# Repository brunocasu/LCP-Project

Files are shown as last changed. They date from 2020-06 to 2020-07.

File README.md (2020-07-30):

# Low-Cost Cubesat Prototype (LCP)
(EN) This repository contains the Hardware and Software Projects to construct and operate a low cost nanosatelite prototype (LCP) developed by the electrical engineering students at the Centro Universitário FEI (Brazil), as part of the Electrical Engineering Bachelor's Thesis Project.

(PT) Este repositório comporta os Projetos de Hardware e Software para construção e operação de um protótipo de baixo custo de nanosatélite (LCP) desenvolvido pelos alunos de engenharia elétrica do Centro Universitério da FEI, como parte do projeto de conclusão de curso de Bacharel em Engenharia Elétrica.

## Hardware Project for the LCP platform
(EN) The hardware project comprehends electrical schematics, PCB designs as well as the BOM (Bill of Materials) intended for its construction.

(PT) O projeto de hardware compreende os esquemas elétricos, design das PCBs e também seu BOM (Lista de Materiais) destinados para sua construção.

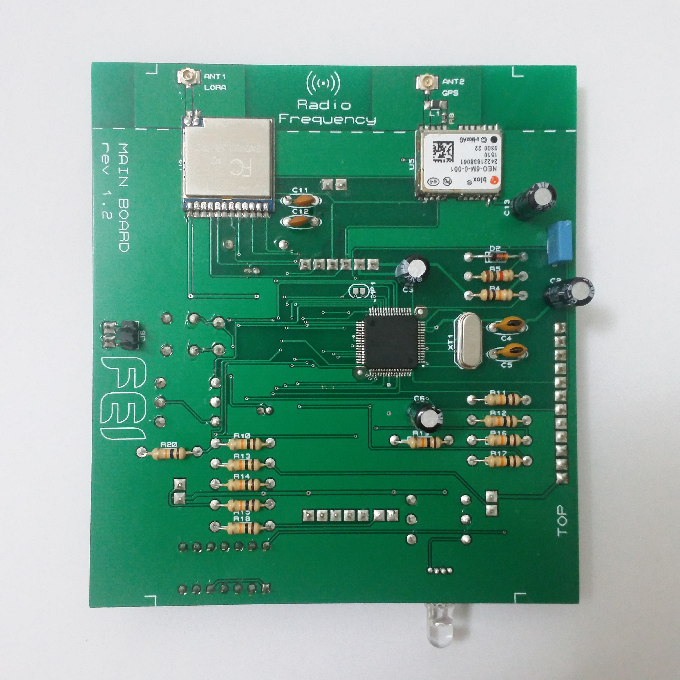
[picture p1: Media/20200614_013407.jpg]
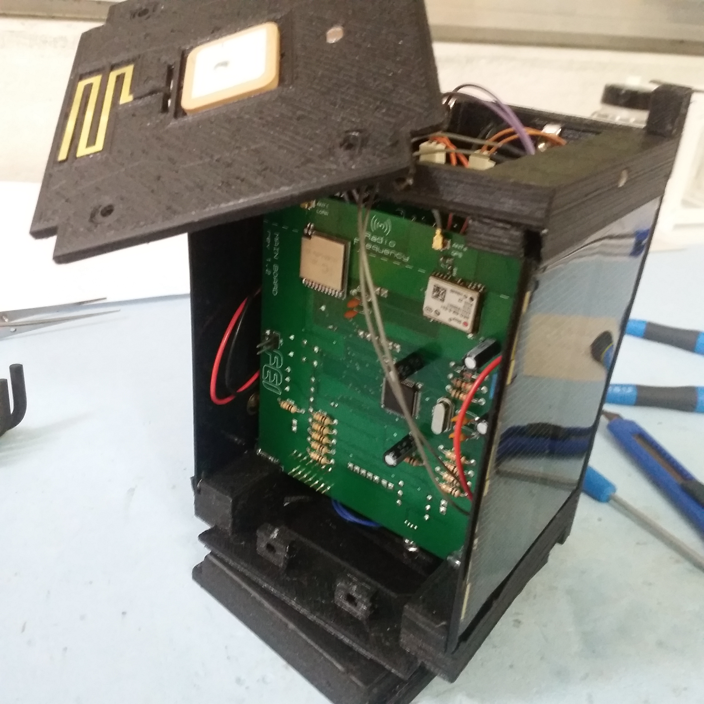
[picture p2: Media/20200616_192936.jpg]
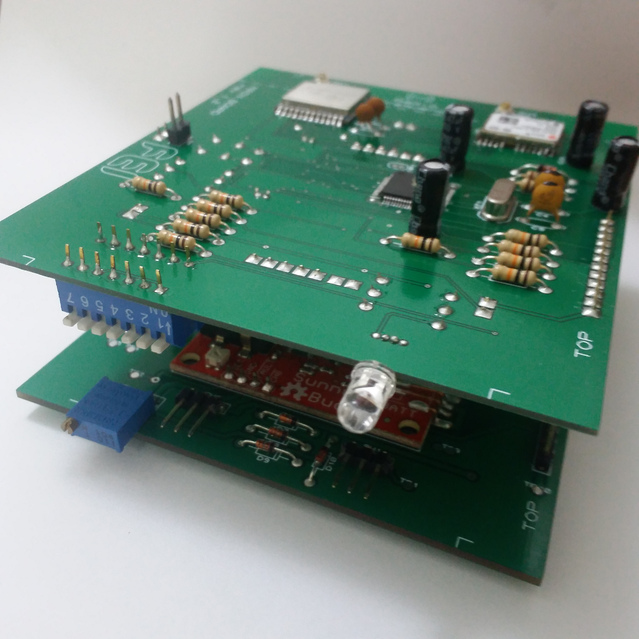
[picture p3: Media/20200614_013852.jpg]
  

## Flight Software for the LCP platform
(EN) The target MCU is the Renesas RL78 - R5F100LE, using the RL78 IAR programming and development tool (IAR IDE for the RL78).
In addition the ground station software is available to RaspberryPi and OrangePi platforms (tests were performed using a Pi Zero W and OrangePi One models).

(PT) O MCU objetivo de utilização foi o Renesas RL78 - R5F100LE, havendo sido utilizado o RL78 IAR para fins de programação e desenvolvimento (IAR IDE for the RL78).
Ainda, o software da estação terrena encontra-se disponível para as plataformas RaspberryPi e OrangePi (testes realizados utilizando os modelos Pi Zero W e OrangePi One).

Execution Example:
```
>>> import lcp

LCP script has started.
Type in:
lcp.diconnect() to disconnect
or CTRL+C to exit.

SX1276 Configuration OK
FLOOR RSSI: - 44.0 dBm

>>> lcp.send_sensor_read ()

INFORMATION FRAME SENT: REQUEST SENSOR READINGS
SEQUENCE NUMBER N(R): 0x1
WAITING FOR REPLY...

MESSAGE RECEIVED (RESPONSE)
REPLY OF INFORMATION FRAME FROM: FEILCP | SEQUENCE N(S): 0x1 | PAYLOAD CODE: 0xa1
SENSORS READING REPLY:
NTC0:             21.81      C
NTC1:             23.30      C
LDR0:             3.13       lux
LDR1:             6.18       lux
LDR2:             2.20       lux
LDR3:             0.09       lux
LDR4:             1.30       lux
LDR5:             4.13       lux
VOLTAGE:          3.28       V
CURRENT:          2.10       mA
BMP280 Temp:     32.04      C
BMP280 Pres:     175.11     kPa
BMP280 Pres:     1.31       mmHg
TIME TO RESPOND: 46.9 ms
RECEIVED SIGNAL STRENGTH INDICATION: - 55.5 dBm
******************************************************************
```

Demonstration: (Watch on YouTube)
Low-Cost Cubesat (https://youtu.be/lgCKG8bld8Y "Low-Cost Cubesat Prototype - Click to Watch!")

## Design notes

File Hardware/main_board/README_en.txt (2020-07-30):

---------------------------------------README----------------------------------------
This schematic is part of the LCP project

---------------------------------------AUTHOR----------------------------------------
@Author		Bruno Duarte

---------------------------------------VERSION---------------------------------------
@version	main_board_v1.x
@brief		main board hardware project

v1.0	Original project for professional manufacturing
v1.1	Simplified project for home made production
v1.2	Dimensional changes to adequate for the available production method

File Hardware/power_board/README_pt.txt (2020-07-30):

---------------------------------------README----------------------------------------
Este esquemático é parte do projeto LCP

---------------------------------------AUTHOR----------------------------------------
@Autor		Bruno Duarte

---------------------------------------VERSION---------------------------------------
@versão		power_board_v1.x
@descrição	projeto PCB da placa de potência

v1.0	Projeto original para produção profissional
v1.1	Projeto simplificado para produção artesanal
v1.2	Alteração de dimensões para adequação ao processo de fabricação disponível

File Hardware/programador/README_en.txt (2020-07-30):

---------------------------------------README----------------------------------------
This schematic is part of the LCP project

---------------------------------------AUTHOR----------------------------------------
@Author		Bruno Duarte

---------------------------------------VERSION---------------------------------------
@version	programador_v1.2
@brief		programmer board hardware project

----------------------------------------NOTES----------------------------------------
#1 Revised project for professional manufacturing

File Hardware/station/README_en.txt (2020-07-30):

---------------------------------------README----------------------------------------
This schematic is part of the LCP project

---------------------------------------AUTHOR----------------------------------------
@Author		Bruno Duarte

---------------------------------------VERSION---------------------------------------
@version	station_v1.2
@brief		shield project for incorporate LoRa on RaspberryPi/OrangePi

----------------------------------------NOTES----------------------------------------
#1 Revised project for professional manufacturing

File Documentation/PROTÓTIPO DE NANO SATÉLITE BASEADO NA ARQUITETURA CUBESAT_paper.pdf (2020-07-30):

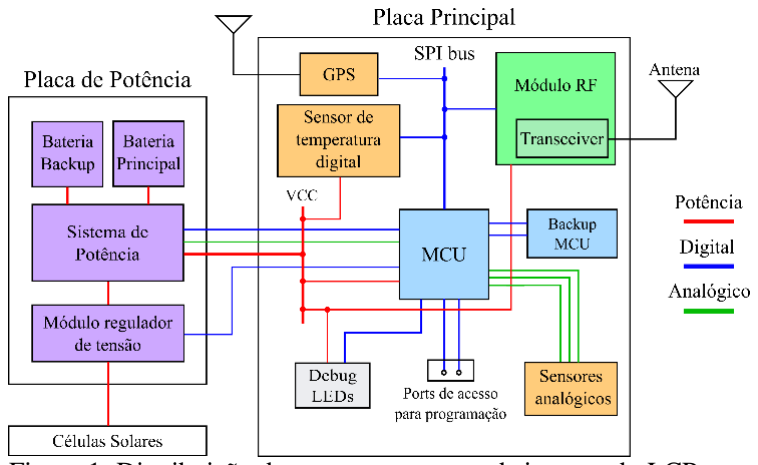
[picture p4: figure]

São Bernardo do Campo – 2020

## PROTÓTIPO DE NANO SATÉLITE BASEADO NA ARQUITETURA CUBESAT PARA RADIOCOMUNICAÇÃO

Bruno Augusto Casu Pereira de Sousa, Bruno Duarte dos Santos, Rodrigo Yudji Katagiri de Oliveira, Victor Garcia Palacios Centro Universitário FEI

Resumo: O avanço das novas tecnologias do ramo aeroespacial foi impulsionado de forma significativa pela evolução dos sistemas de telecomunicação, garantindo aos satélites modernos grande capacidade computacional, mas com a vantagem de miniaturizar os dispositivos, reduzindo os custos das missões. Nesse contexto, o desenvolvimento do padrão CubeSat pela NASA permitiu a expansão de novos estudos e inovações na área, principalmente para as instituições acadêmicas e de pesquisa, ao passo que o modelo permite implementações de baixo custo e
arquiteturas | simplificadas. | O | objetivo | do | projeto
apresentado é estudar e implementar a arquitetura CubeSat no desenvolvimento de um protótipo de nano satélite, designado como Low Cost CubeSat Prototype (LCP). Como resultado, será apresentado um sistema independente com um módulo de comunicação em radiofrequência, permitindo o controle do protótipo e monitoramento dos dispositivos de telemetria por um conjunto de computadores remotos.

### 1. Introdução

Com o aumento da relevância de novos projetos de CubeSats por universidades, e a acessibilidade em relação aos custos de produção e lançamento, comparado a satélites convencionais, se vê um aumento no interesse do lançamento deste formato de satélite. Com isso, a necessidade de uma prova de conceito em relação ao desenvolvimento e produção dos satélites de classe pequena (nano satélites e micro satélites) utilizando tecnologias comerciais comuns se tornou uma necessidade, além de proporcionar diversas inovações na área.
Levando em consideração que um projeto de Cubesat normalmente possui uma duração de 18 a 24 meses para ser desenvolvido, montado, testado e entregue para lançamento [1]; e envolve investimentos elevados, atingindo até 250 mil reais, uma abordagem diferente foi usada na concepção do projeto, visando a produção de uma plataforma de desenvolvimento, que pudesse ser expandida.
O protótipo concebido no projeto então foi designado como Low Cost CubeSat Prototype (LCP), e envolveu um tempo de produção relativamente menor, em torno de 12 meses, além do custo ser reduzido para 3 mil reais, algo mais acessível para instituições de ensino no Brasil. Devido ao tempo e o custo serem menores em comparação ao comum, foi necessário realizar certas abordagens não-convencionais, como o uso de componentes COTS além de métodos para prototipagem simplificados. Portanto, para a composição do LCP foram incorporados módulos de desenvolvimento do segmento de IoT (rádios e sensores), assim como placas de circuito impressas que possam ser fabricadas em fresas de gravação.
Mesmo com certas limitações, ainda se teve um cuidado de seguir parâmetros da NASA para o desenvolvimento do
LCP, | assim | extraindo | de | componentes | eletrônicos
convencionais o máximo possível para se obter uma plataforma com comunicação em Radiofrequência (RF) e com suficiente autonomia. Ainda foram implementados sistemas de redundância no computador de bordo, com backup de CPU, e no sistema de alimentação, utilizando duas baterias. Para uma rápida prototipagem e uma modularidade do sistema, sua parte mecânica foi produzida por impressoras 3D, ainda seguindo os guias de design padrão, mas com certas adaptações e optimizações para os componentes, assim como um nível de flexibilidade para futuras modificações.
Para garantir o funcionamento do sistema geral do LCP e demonstrar sua eficiência, ainda foram realizados certos testes de bancada, focando principalmente na operação do software de voo e comunicação com a estação terrena, demonstração da potência efetiva das células solares e da autonomia das baterias, assim como as funcionalidades dos sistemas de redundância. Nos itens abordados neste texto,
serão | descritos | o | desenvolvimento | e | as | soluções
apresentadas para a plataforma desenvolvida, assim como os testes providenciados.

### 2. Estrutura geral e hardware mecânico

A composição e distribuição dos subsistemas do protótipo foram baseadas em estruturas previamente definidas nas especificações e outros projetos de CubeSat que foram desenvolvidos e testados [2][3]. Essencialmente o sistema de um nano satélite deve conter cinco funções, em adição à estrutura mecânica, que então definem a plataforma: Subsistema de alimentação, Dispositivos de telemetria, Subsistema de comunicação, CPU e Controle de temperatura. No caso específico do LCP, o controle de temperatura das baterias foi repassado para o computador central, de forma a simplificar o sistema de controle exigido.

Figura 1: Distribuição dos componentes e subsistemas do LCP.

Na Figura 1 é possível notar a distribuição dos componentes na arquitetura do LCP, compondo os subsistemas básicos da plataforma. A integração dos componentes foi complementada com o desenvolvimento de um frame customizado para o projeto.

A estrutura mecânica foi baseada nos aspectos e definições da NASA em relação ao formato e composição do frame para o CubeSat [4]. O padrão então denomina o tamanho de um único cubo a unidade U, onde um CubeSat 1U, ou 1 cubo, possui 100 milímetros por 100 mm por 100 mm. As demais denominações (2U, 3U) possuem um incremento de 100 mm na altura (eixo z) para cada adição de uma unidade. Estas derivadas do tamanho U, no entanto, requerem invariavelmente que uma de suas faces possua 100 x 100 milímetros, devido ao modo da construção do instrumento de lançamento dos satélites, este denominado Poly-Pico Orbital Deployer ou P-POD, que possui um espaço interno de 100x100x300 milímetros.
Considerando | que | o | frame | do | protótipo | foi
desenvolvido com certas adaptações, o design final da estrutura mecânica do LCP acabou por não atender rigorosamente os padrões de altura, denominados pela unidade U. Isso ocorreu por conta das placas solares adquiridas, além da necessidade de utilizar placas PCB maiores para comportar os módulos usados. Em todo caso, as medidas de larguras, sendo as dimensões críticas, mantiveram o padrão de 100 mm de lado, ainda definindo o protótipo na classe de nano satélites. Eventualmente um aumento na classe do protótipo para 2U pode ser considerado para futuras expansões, de forma a manter o protótipo nos padrões requeridos.

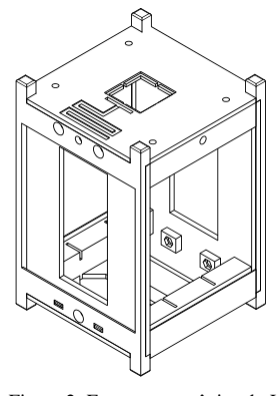
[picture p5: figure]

Figura 2: Estrutura mecânica do LCP.

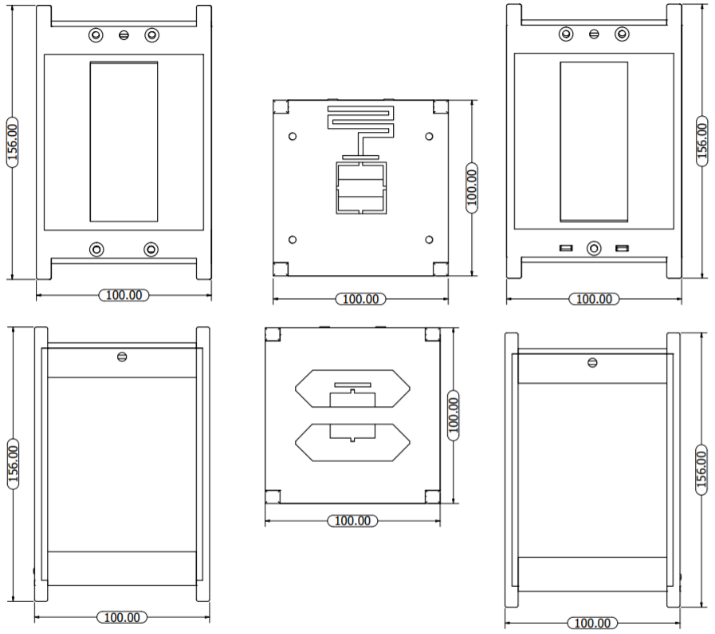
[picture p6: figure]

Figura 3: Vista das peças do frame customizado do LCP.

Os suportes das partes eletrônicas nesse design foram feitos de modo em que a montagem fique unificada, além de otimizar o centro de massa do dispositivo e seu espaço interno. Componentes de RF que necessitam ficar na superfície externa do cubo, como as antenas, se encontram em recessos no topo, sendo mantidos presos pelo próprio material. Essa estratégia também foi usada para posicionar as placas solares, que ficam ao centro das áreas laterais, e as placas principais com seus standoffs embutidos, ajudando também na rigidez mecânica do projeto.
O design mecânico em sua totalidade foi confeccionado em impressoras 3D, por sua velocidade de prototipagem combinadas a sua alta precisão, habilitando assim mudanças frequentes de medidas e designs. O material usado para sua composição foi o Tritan HT, um copoliester 3d fila, possuindo uma alta dureza e resistências a temperaturas, este sendo um outro desvio as recomendações da NASA que indica a construção de sua estrutura por alumínio 7075, 6061, 5005 ou 5052.

### 3. Subsistema de potência

O sistema de potência do LCP consiste em uma junção de quatro placas solares ligadas em paralelo e duas baterias de polímero de lítio, também denominadas Lipo. As partes então foram associadas ao módulo regulador de tensão SunnyBuddy da SparkFun [5], que implementa tecnologia de Maximun Power Point Tracking (MPPT) para maximizar a eficiência das células solares em conjunto com o sistema de baterias.
O módulo então provê as funcionalidades necessárias para o gerenciamento do fornecimento de energia ao sistema principal, de forma a garantir o funcionamento da plataforma. A placa SunnyBuddy também possui circuito de proteção para as baterias inseridas no sistema de potência, sendo de grande importância para a utilização de baterias com lítio em sua composição, visto que uma falha poderia causar sobrecargas, danificando o hardware.

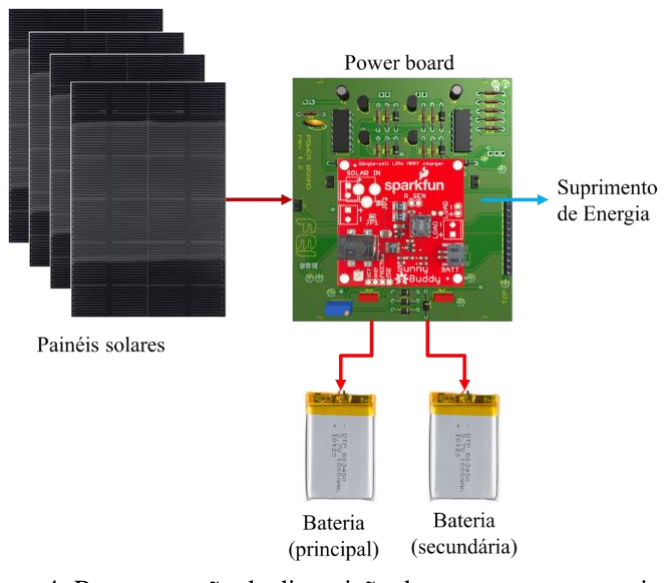
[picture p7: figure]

Figura 4: Representação da disposição dos componentes no sistema de potência.

As baterias escolhidas têm carga de 2600mAh, e foram incorporadas na placa de potência por um circuito de troca dedicado, desenvolvido especificamente para a aplicação no LCP. Essa implementação garante o funcionamento em redundância, onde a bateria secundaria se encontra em cold standby, e, caso ocorra uma eventual falha que danifique a bateria principal ou se sua eficiência caia drasticamente se tem a troca para a bateria secundaria, assim estendendo a longevidade da bateria assim como a sua resistência a falhas. O circuito ainda disponibiliza ao controlador da estação a possibilidade de atuar remotamente na supervisão e troca das baterias do sistema de potência, elevando a disponibilidade da plataforma.

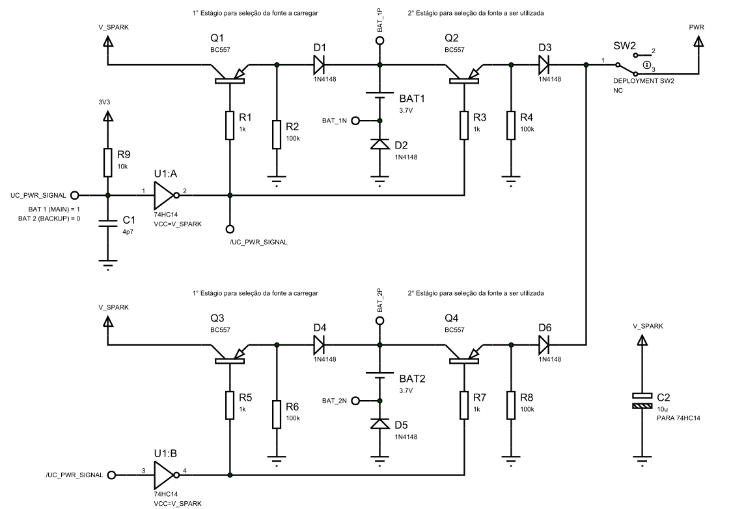
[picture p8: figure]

Figura 5: Circuito de troca de baterias.

Dadas as considerações da implementação do sistema de alimentação, a placa PCB foi confeccionada para atender os requisitos de corrente necessário e comportar os módulos usados no sistema com as células solares e as baterias. A Figura 6 ilustra a placa desenvolvida para o LCP com os componentes inseridos. Nota-se ainda que foi utilizado um barramento de pinos para garantir a conexão dos pinos de potência com a placa principal, onde os outros subsistemas e dispositivos se encontram.

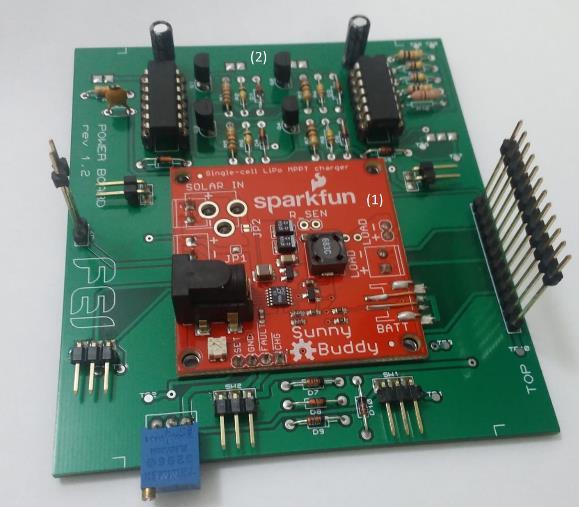
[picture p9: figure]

Figura 6: Placa de potência do LCP.

### 4. Dispositivos de telemetria

Como forma de demonstrar a manutenção e supervisão dos subsistemas agregados no LCP, cinco tipos de sensores foram dispostos: temperatura, pressão, luminosidade, tensão e corrente. O principal componente de telemetria do protótipo é o sensor digital de temperatura BMP280 da Bosch [6], que foi implementado para prover leituras, com precisão de 0,01 °C, da temperatura do ambiente. As leituras e a programação desse dispositivo são realizadas pela interface serial do sensor, através de um barramento SPI (em concordância com a arquitetura computacional do LCP). O

BMP280 ainda prove leitura de pressão do ambiente, sendo um complemento interessante para a avaliação das condições de operação do protótipo nos testes.
Além do sensor digital, um sensor de corrente e outro de tensão foram usados para monitorar o comportamento do sistema, em específico das condições da placa de potência. Esses sensores providenciam leituras analógicas ao computador central do nível de tensão fornecido à placa principal e a corrente de operação, e tem relevância na garantia da integridade dos componentes usados na alimentação. Além disso, as baterias da placa de potência são monitoradas com sensores analógicos de temperatura (NTC), de forma a os controladores da estação no solo as condições de operação.
O subsistema de telemetria ainda foi complementado com a inserção de sensores e luminosidade (LDR) nas laterais do cubo, de forma a identificar as regiões com maior intensidade luminosa. Esses sensores têm relevância pois disponibilizam dados de luminosidade que podem ser computados para uma análise estatística do comportamento de carga das baterias. Os dados de luminosidade então fazem parte do Payload do LCP.
Finalmente ainda foi avaliado o uso de um sistema de GPS em conjunto com o módulo de comunicação, adicionado mais informações relevantes no link com as estações. O GPS então foi adicionado à plataforma como complemento do Payload disponibilizado.

### 5. Subsistema de comunicação

O módulo de comunicação do CubeSat compõe o subsistema mais crítico do projeto, considerando que seu funcionamento deve prover uma comunicação estável e robusta com as estações, além de permitir o envio de uma taxa considerável de dados de forma a atender a composição do payload da plataforma [7]. Para o sistema de comunicação do LCP, sua composição foi modelada para o uso de um transceiver LoRa de baixo consumo SX1276, da Semtech [8][9]. O rádio está presente em um módulo wireless da NiceRF, otimizado para operação em 915 MHz [10]. Além da estrutura de RF, o módulo usado facilita a integração desse subsistema com o computador central do LCP, visto que o componente disponibiliza uma interface de acesso serial aos registradores do SX1276, através de um barramento SPI, assim como o sensor digital do subsistema de telemetria.
Com isso, os parâmetros do rádio são definidos com a escrita nos registradores do SX1276, através desse barramento serial; em adição, os dados da comunicação também são transmitidos pelo SPI, usando uma fila FIFO no DFE do rádio para garantir a eficiência do transceiver na composição e envio dos pacotes, assim como no recebimento e informe da chegada de mensagens.
Para a comunicação do LCP , o rádio foi configurado com a maior potência de transmissão, em 20 dBm, além do uso do modem FSK do transceiver. A taxa padrão de transmissão foi estabelecida para 4,8 kbps, com separação de portadoras em 5 kHz. Nessa configuração, portanto, a sensibilidade esperada então se mantém em torno de -110 dBm, permitindo um alcance considerável para a comunicação do protótipo.

Além dos parâmetros de transmissão do rádio, o SX1276 permite o envio das informações em diferentes formatos. O link com as estações remotas foi implementado usando um protocolo com pacotes de tamanho fixo em 64 bytes. Nesse pacote ainda foi habilitado a implementação de um código de correção de erros CRC pelo transceiver, além da utilização de uma palavra de sincronização e redundância 4/5. Com isso a comunicação entre os rádios foi mantida com considerável robustez e taxa de transmissão de dados. Em complemento com o pacote do SX1276 o LCP ainda usa um protocolo de acesso de link. Devido ao tempo disponível para desenvolvimento do software, foi decido utilizar uma implementação própria do protocolo de link de acesso AX.25 [11], extraindo as características principais de sua estrutura, e adaptando certos aspectos para o subsistema de comunicação do LCP. Dessa forma, a camada de acesso permite o envio de endereços, bytes de controle e supervisão, além de números sequenciais nas mensagens, atribuindo boa confiabilidade ao link do protótipo com as estações remotas. Na figura a seguir está exemplificado uma sequência de mensagens padrão no link, ilustrando a organização das numerações das mensagens a partir do protocolo AX.25 adaptado.

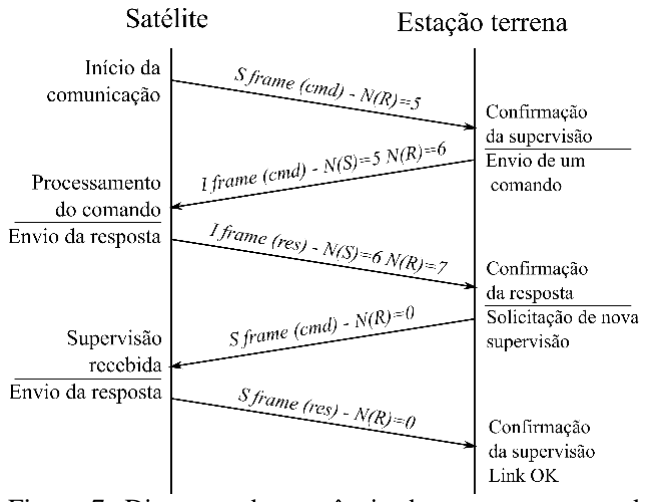
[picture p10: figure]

Figura 7: Diagrama de sequência de mensagens trocadas no link de comunicação entre o LCP e a estação terrena.

No contexto da comunicação do LCP, ainda foi elaborado uma série de funções adicionais, sendo inseridas no espaço de informação disponível no frame do protocolo de acesso. Um segundo protocolo então foi implementado (LCP Application Protocol, LAP), providenciando uma camada de aplicação à plataforma. Essas funções extras permitem a obtenção das informações do satélite, leituras de sensores, monitoramento do sistema de potência, além de uma função de envio de mensagens de texto entre estações remotas.

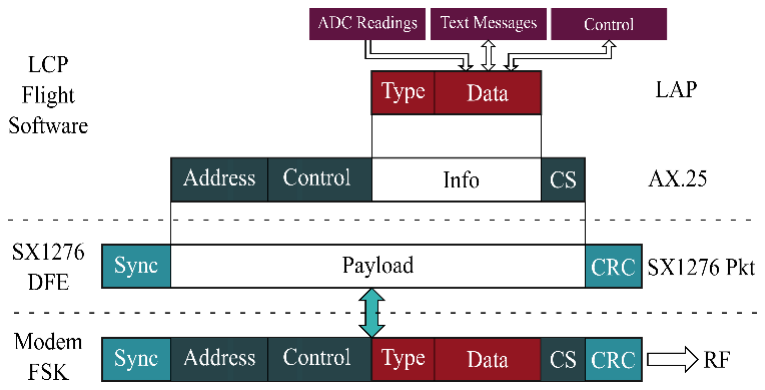
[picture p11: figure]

Figura 8: Divisão das camadas de comunicação o LCP.

Na Figura 8 então é ilustrado o desenvolvimento das camadas de comunicação do protótipo, considerando em última instância a camada física do sinal modulado em FSK e transmitido em RF.
Nota-se ainda na figura que as camadas inferiores são implementadas no hardware do módulo de comunicação usado, ao passo que as camadas superiores da comunicação são resolvidas pelo software de voo do LCP. Com isso a supervisão e comunicação do dispositivo em operação é garantida, considerando que o protótipo envia mensagens regularmente às estações. Da figura ainda é possível notar, ao final do processo, a estrutura final do pacote; que então deve ser modulado em FSK pelo transceiver e enviado às estações.
Como complemento ao hardware do rádio, uma antena monopolo foi adquirida para inserção na face superior externa do cubo, de forma a maximizar o ganho. Essa antena ainda possuiu dimensões reduzidas e montagem de forma plana, facilitando sua inserção no frame do LCP.

### 6. Computador central e software de voo

Como componente central de controle da plataforma, o LCP faz o uso de um microcontrolador, inserido em uma arquitetura de computação em estrela [3], mantendo o Computador de bordo como dispositivo central, ligado aos subsistemas periféricos. O MCU usado no projeto foi escolhido considerando as grandes restrições de consumo de corrente, além da necessidade das interfaces seriais e conversores ADC, de forma a contemplar todas as necessidades da arquitetura estabelecida para o protótipo.
O componente escolhido foi então o modelo RL78 R5F100LG, da fabricante Renesas [12][13]. Esse MCU é da família Ultra Low Power de microcontroladores, e possuiu
características | computacionais | razoáveis | para | o
desenvolvimento e testes da plataforma, como: RAM de 12 kB e memória flash programável de 128 kB, mantendo um consumo de corrente de 4,6 mA na operação normal. Como forma de garantir a confiabilidade do sistema de controle, essa CPU foi instalada com um segundo RL78 em redundância, de forma que caso ocorra uma falha no computador principal, o MCU de backup passa a atuar no controle do sistema.
Da interface do RL78 serão usados ainda um canal serial da Serial Array Unit (SAU) para o SPI da plataforma, e 10 canais ADC para o uso dos sensores analógicos disponíveis.
Considerando | a | disponibilidade | do | sistema | de
computação, o software de voo foi desenvolvido para garantir a manutenção dos dispositivos, o controle dos sistemas e a comunicação do satélite. A linguagem C de programação foi amplamente usada no projeto, em conjunto da plataforma de desenvolvimento IAR IDE [14], específica para os microcontroladores da família RL78.
O software de voo então contempla um driver desenvolvido para configuração e controle do SX1276, um driver para implementação do protocolo de acesso AX.25, um driver para os sensores e dispositivos de telemetria e uma máquina de estados geral (FSM). A FSM implementada então tem o propósito de realizar as chamadas das funções dos drivers realizando as transições dos estados na comunicação (transmitindo ou recebendo) além de manter a supervisão do funcionamento dos sistemas. Os estados definidos na FSM são ilustrados na figura a seguir:

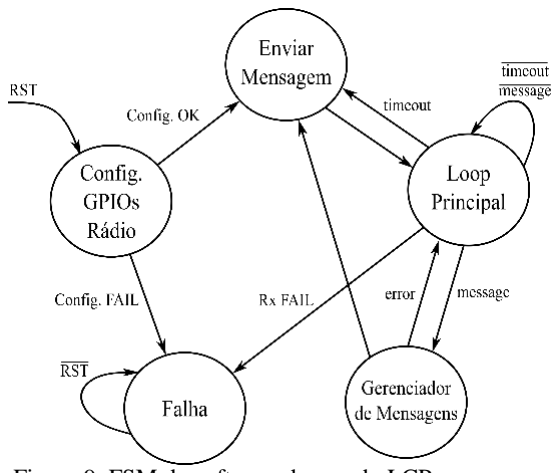
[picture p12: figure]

Figura 9: FSM do software de voo do LCP.
O software, em sua operação normal, inicia o sistema com a configuração dos registradores e periféricos ligados ao computador central (timers, ADCs, canais seriais e interrupções do RL78), além da habilitação dos GPIOs do MCU e a configuração geral dos parâmetros do rádio. Caso essa operação falhe, o sistema é levado a um estado de falha crítica, desabilitando as funções de controle até que um reset externo seja executado. No caso de as configurações serem realizadas com sucesso, o software deve então passar para o estado de envio de mensagens, transmitindo o primeiro comando de supervisão, o que indica as estações que o satélite está pronto para operar. Após o envio dessa primeira mensagem, a máquina de estados passa para o loop principal, onde o rádio é configurado para o modo receptor, aguardando os comandos da estação.
Nesse estado, um contador é ativado, realizando um incremento a cada um segundo, onde, em paralelo, o software verifica a integridade dos sistemas de alimentação. Quando o contador do loop atinge um valor determinado (timeout), uma mensagem de supervisão é automaticamente gerada, identificando que o dispositivo ainda se mantém ativo. Caso ocorra uma falha ou mal funcionamento na alimentação do sistema, a placa da Sparkfun informa o controlador central, que altera o conteúdo das mensagens regulares em sua rotina de supervisão, possibilitando aos controladores que atuem na plataforma com o envio de comandos de controle de hardware.
Em outro caso, onde o sistema ainda está no loop principal, o rádio pode receber uma mensagem proveniente de uma estação. Nessa situação, a máquina de estados é informada através de uma interrupção de hardware (sinal gerado por pinos digitas da interface do SX1276), que identifica o recebimento de um pacote pelo rádio. Assim, o loop é interrompido e a FSM passa para o estado gerenciador de mensagens. Nesse estado, o sistema faz a leitura dos bytes da FIFO do SX1276, recuperando a mensagem recebida e identificando o comando da camada de aplicação. Para tanto, a decomposição das camadas de comunicação competentes ao software é realizada em tempo de operação. Após a identificação, o sistema deve providenciar o conteúdo adequado para a resposta a estação de origem da mensagem. Ao término do processamento do estado gerenciador de mensagens, o sistema altera o rádio para o modo transmissor, e envia a resposta às estações. No caso e requisição de leituras ou outros comandos da camada de aplicação que exijam a atuação do LCP, o dispositivo então executa a ação recebida antes de retornar ao loop principal, sendo necessário em alguns casos, executar a tarefa antes do envio da resposta.
O software desenvolvido | então | implementa | as
funcionalidades básicas de supervisão e controle na plataforma, garantindo a disponibilidade e confiabilidade do sistema em órbita.
Com a correta disposição dos subsistemas apresentados, a placa principal do LCP foi desenvolvida de forma a comportar o sistema computacional, os dispositivos de telemetria e o módulo de comunicação, permitindo a programação do MCU e proporcionando as conexões com os outros dispositivos (barramento SPI, sinais digitais e analógicos). A placa ainda deve conter dois circuitos de casamento de impedâncias, de forma a rotear o sinal em RF da saída do transceiver do SX1276 para o conector da placa ligado à antena principal, assim como o sinal da antena do GPS para o conector do módulo.

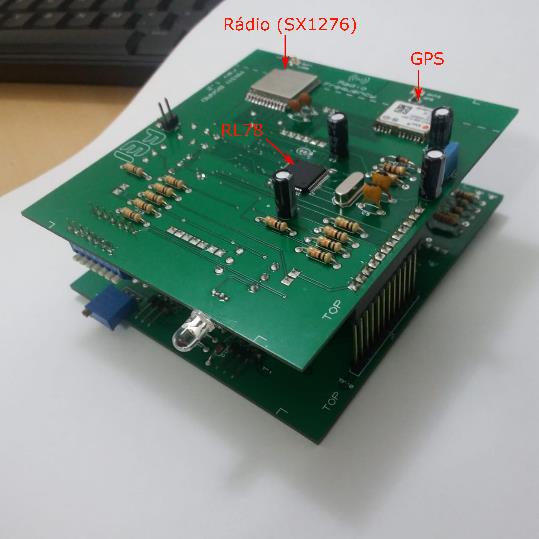
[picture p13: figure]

Figura 10: Placa principal do LCP.

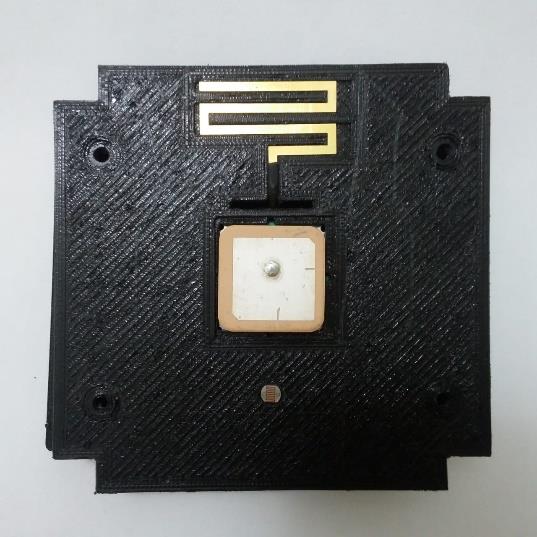
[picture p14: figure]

Figura 11: Sistema de antenas conectadas à placa principal (antena do GPS ao centro, antena monopolo para o LoRa 915 MHz na parte superior).

### 7. Integração e testes

Com a produção e configuração do hardware e software da plataforma definidas, o LCP passou para o estágio de montagem e integração. As placas então foram associadas ao frame com as devidas ligações e interconexões. As figuras a seguir ilustram o processo de montagem do LCP.

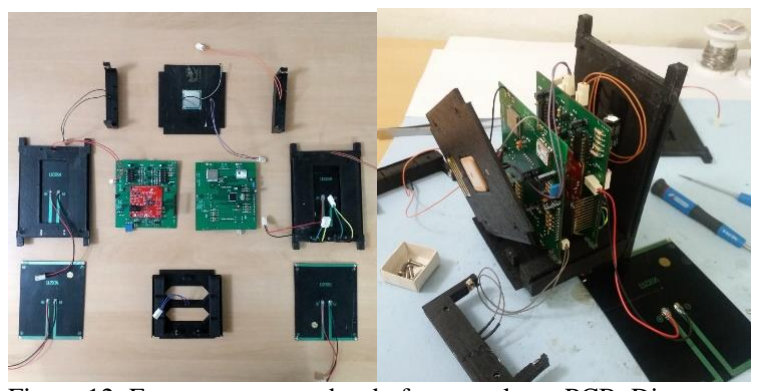
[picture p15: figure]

Figura 12: Esq. peças separadas do frame e placas PCB. Dir. inserção das placas no frame e conexão com as placas laterais

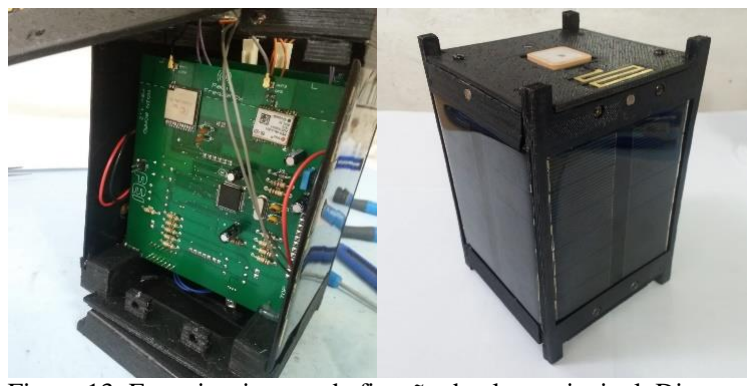
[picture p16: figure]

Figura 13: Esq. vista interna da fixação da placa principal. Dir. montagem final do LCP.

A montagem dos componentes requerer certo cuidado no roteamento das conexões com as placas laterais do cubo, considerando que o cabeamento foi disposto nos espaços laterais recuados. Assim, a placa de potência se mantém ligada às quatro células solares posicionadas nas laterais. A placa principal é ligada por um barramento de pinos à placa de potência, providenciado os sinais de terra e VCC, além de pinos digitais e analógicos para a integração do subsistema de potência com o sistema de controle do computador de bordo e software de voo.
Como teste inicial foram avaliados os parâmetros de autonomia, considerando o consumo de corrente pelos dispositivos operando. Deve ser levado em conta ainda os valores de disponibilidade de fornecimento de energia pelas placas solares, definido os ciclos de carga e descarga das baterias. Dessa forma, a composição da plataforma apresentou o seguinte comportamento:
Parâmetro avaliado | Valor
Consumo de corrente no modo receptor | 75,0 mA
Consumo de corrente no modo transmissor | 150 mA
Consumo médio no tempo (10 s em Rx / 0,5 s em Tx) | 78,6 mA
Carga total da bateria | 2600 mAh
Corrente fornecida pelas células solares | 112 mA
Autonomia da bateria em operação padrão | 31,8 h
Tabela 1: Parâmetros do sistema de potência obtidos nos testes da plataforma.

Com os dados da tabela é possível avaliar a disponibilidade do sistema, concluindo sobre a autonomia do dispositivo, que se manteve coerente com o esperado para o projeto do subsistema de potência. Como forma de aprimorar a plataforma, placas solares com maior eficiência, além de baterias com maior carga pode ser facilmente integrada ao hardware, de forma a substituir os componentes simplificados usados na primeira versão do LCP.
Para uma segunda avaliação, o software foi testado estabelecendo a comunicação com a estação remota. A configuração das estações foi definida com o uso de um hardware mais potente em relação ao sistema computacional do LCP. Foi implementado um sistema baseado na plataforma Raspberry Pi, usando o modelo Pi Zero W, em conjunto com o módulo LoRa 915 MHz. Para a configuração dos parâmetros do rádio nessa plataforma, um software em Python foi de desenvolvido, e estrutura composição espelha o funcionamento do protótipo, implementando configurações idênticas ao usado no LCP. Além disso um hardware simplificado também foi desenvolvido para a aplicação da estação (Shield para comportar o rádio e um barramento compatível com a disposição dos pinos da RaspberryPi). Para o rádio da estação, uma segunda antena foi testada para o módulo LoRa foi testada (dipolo curto), de forma a avaliar outras possibilidades de hardware para o protótipo.
Assim, foi possível estabelecer o link de rádio, enviando e recebendo mensagens de supervisão e controle. Apesar das configurações desenvolvidas para o RaspberryPi, os testes iniciais foram realizados com um OrangePi, sendo um dispositivo similar.

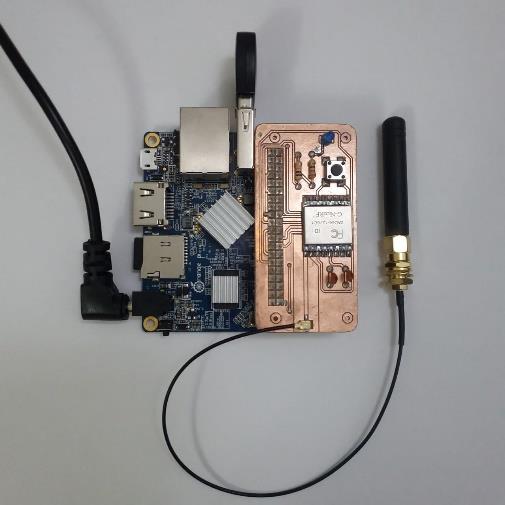
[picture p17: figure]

Figura 14: Configuração da estação remota para
os testes de comunicação com o LCP.

As ilustrações seguintes mostram a interface da estação remota do projeto, sendo usado o sistema operacional do RaspberryPi (Linux) para gerar o texto. Com essa montagem então é possível enviar comando diretamente dessa interface, que exibe as mensagens recebidas do satélite, ao passo que as camadas de acesso e aplicação também são inseridas no software da estação, recuperando os dados enviados pelo LCP.

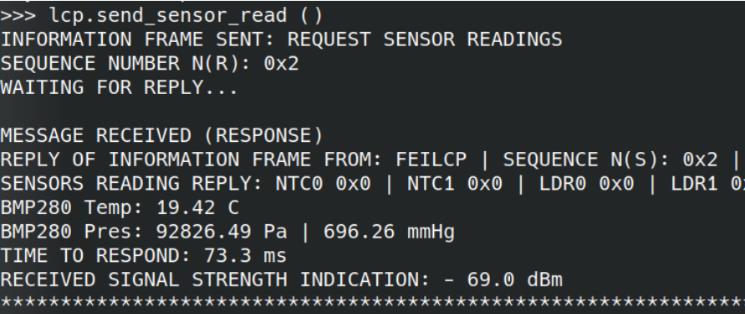
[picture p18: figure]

Figura 15: Comando de leitura de sensores.

O comando exemplificado na Figura 15 mostra o envio de uma requisição ao LCP, e a resposta recebida na interface da estação. Dos dados obtidos nota-se as leituras de temperatura e pressão do sensor digital usado (sensores analógicos e o GPS estavam desabilitados nesse teste). Os resultados na interface então apresentam a capacidade de controle e supervisão da plataforma desenvolvida, visto que para se obter as leituras, o LCP deve desempacotar a mensagem enviada, processar o tipo de comando e atuar na reconfiguração do software. Além dessas funções para se obter as leituras, o sistema deve acessar os registradores do BMP280 e obter as leituras binárias através do barramento SPI, sendo que ao final desse processo, o software de voo irá montar frames do protocolo AX.25 adaptado e enviar a sequência de bytes para o rádio, que irá empacotar e transmitir a resposta. Esse comando então demonstra todo o processo de controle de software e hardware feito pelo protótipo, e acionado remotamente pela estação com o envio de comandos desenvolvidos para o link.

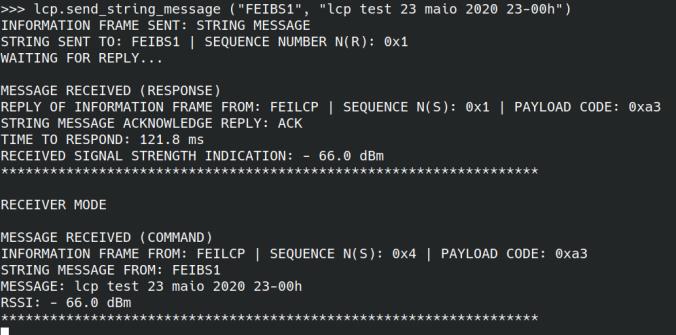
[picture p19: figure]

Figura 16: Comando de envio de mensagens de texto.

Na Figura 16 outro tipo de comando é demonstrado, onde uma mensagem de texto foi originada na estação de endereço 'FEIBS', e destinada para o mesmo endereço. Da interface é possível notar dois recebimentos na estação, o primeiro é uma Resposta proveniente do LCP identificando que o Comando enviado foi processado (string "ACK"). Em seguida, a estação recebe a retransmissão da string de texto enviada, confirmando a função de comunicação ponto aponto estabelecida na plataforma.
Além das funcionalidades e dados dos comandos, a interface ainda disponibiliza informações relevantes do link, como o tempo de resposta do módulo (121,8 ms em 4,8 kbps) e a intensidade do sinal recebida na estação (-66 dBm). A estrutura dos frames da camada de acesso também fica disposta na interface, mostrando os endereços dos dispositivos que originaram as mensagens, além do número sequencial de controle dos frames, garantindo maior confiabilidade na comunicação.
Dos resultados da capacidade de comunicação, foram extraídos os parâmetros máximos de sensibilidade e taxa de transmissão, esses então sendo, respectivamente, - 96 dBm e 19,2 kbps. Portanto, o módulo de comunicação, além do software de voo se mostraram consistentes com o esperado para o link com o satélite, garantindo uma comunicação estável e com taxas razoes de transmissão de bits e um alcance considerável para o rádio usado.

### 8. Conclusões

O desenvolvimento da plataforma do LCP agregou diversos conceitos usados em projetos da área espacial, de forma que o aprendizado sobre os processos de produção e desenvolvimento proporcionaram a construção de um possível protótipo para futuras aplicações espaciais no Brasil.
Além disso, as implementações foram direcionadas à entrega de uma plataforma confiável e flexível, permitindo sua evolução em versões futuras. O resultado obtido com os subsistemas adaptados ainda demonstra a capacidade razoável do protótipo, visto que os materiais de baixo custo foram suficientes para a prova de conceito envolvendo a produção de um módulo independente que recebe e envia comandos em RF em um determinado link de rádio.
As | soluções | concebidas | no | protótipo | ainda
proporcionaram a abordagem da estrutura e distribuição dos subsistemas de forma particular para o LCP, garantindo uma implementação inovadora, dentro dos limites da capacidade computacional do hardware, do orçamento e da experiência da equipe de produção.
Os testes de bancada do software ainda comprovaram a correta integração dos subsistemas concebidos do projeto do LCP e a disponibilidade da plataforma desenvolvida, bem como sua autonomia e capacidade do link de comunicação. Apesar dos resultados promissores do protótipo, em relação à comunicação e hardware, ainda é necessário uma série de adaptações à plataforma para que ela seja certificada para voo. Deve ser considerando que alterações no frame do cubo sejam feitas, substituindo os materiais empregados no protótipo por ligas metálicas de alumínio, além de alterações nos componentes das placas solares e baterias, garantido maior autonomia e eficiência energética. Em relação ao software de voo, melhorias ainda devem ser feitas para incrementar a supervisão dos equipamentos do nano satélite, além de expandir as funcionalidades de controle e telemetria.
Considerando os devidos complementos de hardware e software atualizado, o protótipo pode então passar para os testes de campo mais desafiadores. Por exemplo, o uso de balões meteorológicos é uma interessante forma de testar o comportamento dos subsistemas em um ambiente diferente. Com isso, o LCP pode futuramente estabelecer um ponto de partida para novos modelos de CubeSat desenvolvidos no Brasil.

### 9. Referências

[1] NASA. CubeSat 101: Basic Concepts and Processes for First-Time CubeSat Developers. 2017.
[2] KHERRAS, A.; ADDAIM, A.; ZANTOU, El B. Design of Low-cost Telecommunications CubeSat-class Spacecraft. Morocco, 2010.
[3] PALMINTIER, B. et al. A Distributed Computing Architecture for Small Satellite and Muilt-Spacecreft Missions. Santa Clara, 2002.
[4] NASA. CubeSat Design Specification. Rev. 13. 20 de fevereiro, 2014.
[5] SPARKFUN. Sunny Buddy Solar Charger V13 Hookup Guide. Manual de operação. Disponível em: <https://learn.sparkfun.com/tutorials/sunny-buddy-solar-charger-v13-hookup-guide-/all>. Acesso em 31 de maio, 2020.

[6] BOSCH. BMP280 Digital Pressure Sensor. Datasheet, revisão 1.14. 5 de maio, 2015.
[7] HENDERSON, P. B. High Data Rate Radio Transmitter for Cube Satellites. Logan, 2009.
[8] SEMTECH. SX1276/77/78/79 - 137 MHz to 1020 MHz Low Power Long Range Transceiver. Datasheet. 5 de agosto, 2016.
[9] SEMTECH. AN1200.19: SX127x Refence Design Overview. Application Note. Revisão 2, dezembro 2014.
[10] NICERF. Lora1276: 100mW Long Range Spread Spectrum Modulation Wireless Transceiver Module. Product Datasheet v2.0. 2016.
[11] BEECH, W. A.; NIELSEN, D. E.; TAYLOR, J. AX.25 Link Access Protocol for Amateur Packet Radio. Version
2.2. 1998.
[12] RENESAS. RL78/G13 User's Manual: Hardware. Rev.3.20. julho de 2014.
[13] RENESAS. RL78/G13 RENESAS MCU. Datasheet. Revisão 3.40. 31 de maio, 2018.
[14] IAR SYSTEMS. IDE Project Management and Building Guide: for the Renesas RL78 Microcontroller Family. Guia do usuário para a plataforma IAR Embedded Workbench. 6. ed. 2019.
[15] ALMEIDA, A. T. Planar Antennas For CubeSat Missions. Dissertação (Mestrado em Engenharia Elétrica). Técnico Lisboa, 2018.
[16] BALANIS, C. A. Antenna Theory: Analysis and Design. 4. ed. New Jersey, 2016.
[17] CHANDRASHEKAR, S. Thermal Analysis and Control of MIST CubeSat. DEGREE PROJECT IN SPACE TECHNOLOGY. Estocolmo, 2016.
[18] FAGUNDES, I. F. Desenvolvimento de Uma Estação Terrena (ET) Para o Nano Satélite Científico Brasileiro -NANOSATC-BR. Santa Maria, junho de 2009.
[19] INPE. Montagem, Integração e Testes de Satélites. Disponível em:
<http://www.lit.inpe.br/pt-br/montagem_integracao_e_testes_de_satelites>. (http://www.lit.inpe.br/pt-br/montagem_integracao_e_testes_de_satelites) Acesso em 27 de abril, 2020.
[20] LATHI, B. P.; DING, Z. Sistemas de Comunicação Analógicos e Digitais Modernos. 4. ed. Rio de Janeiro: LTC, 2012.
[21] MURDOCCA, M.; HEURING, V. Principles of Computer Architecture. 1999.
[22] RICHHARIA, M. Satellite Communication System: Design Principles. 2. ed. 1999.
[23] SEDRA, A. S.; SIMTH, K. C. Microeletrônica. 4. ed. São Paulo: Pearson, 2005.

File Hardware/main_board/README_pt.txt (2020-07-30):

---------------------------------------README----------------------------------------
Este esquemático é parte do projeto LCP

---------------------------------------AUTHOR----------------------------------------
@Autor		Bruno Duarte

---------------------------------------VERSION---------------------------------------
@versão		main_board_v1.x
@descrição	projeto PCB da placa principal

v1.0	Projeto original para produção profissional
v1.1	Projeto simplificado para produção artesanal
v1.2	Alteração de dimensões para adequação ao processo de fabricação disponível

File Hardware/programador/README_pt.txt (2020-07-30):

---------------------------------------README----------------------------------------
Este esquemático é parte do projeto LCP

---------------------------------------AUTHOR----------------------------------------
@Autor		Bruno Duarte

---------------------------------------VERSION---------------------------------------
@versão		programador_v1.2
@descrição	projeto PCB do programador

----------------------------------------NOTES----------------------------------------
#1 Projeto revisado para confecção profissional

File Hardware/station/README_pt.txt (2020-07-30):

---------------------------------------README----------------------------------------
Este esquemático é parte do projeto LCP

---------------------------------------AUTHOR----------------------------------------
@Autor		Bruno Duarte

---------------------------------------VERSION---------------------------------------
@versão		station_v1.2
@descrição	projeto de shield para incorporar módulo LoRa ao RaspberryPi/OrangePi

----------------------------------------NOTES----------------------------------------
#1 Projeto revisado para confecção profissional

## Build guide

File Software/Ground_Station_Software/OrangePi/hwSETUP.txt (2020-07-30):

Configurações de hardware, OrangePi One:

- Kernel habilitado para SPI canal 0: /dev/spidev0.0
- Instalados módulos "spidev" e "OPi.GPIO" em ambas versões do python (v2 e v3)

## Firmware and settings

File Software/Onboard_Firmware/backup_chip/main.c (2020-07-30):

/****************************************************************************/
/*                                                                          */
/* This Source Code Form is subject to the terms of the Mozilla Public      */
/* License, v. 2.0. If a copy of the MPL was not distributed with this      */
/* file, You can obtain one at http://mozilla.org/MPL/2.0/.                 */
/*                                                                          */
/****************************************************************************/

/*
 * This File is part of the LCP project
 */

/**
 * @file main.c
 *
 * @author Bruno Agusto Casu
 *
 * @revisor Bruno Duarte
 *
 * @brief main function and hardware configuration
 */


#include "string.h"
#include "stdio.h"
#include "stdlib.h"
// applilet includes
#include "r_driver/r_cg_macrodriver.h"
#include "r_driver/r_cg_adc.h"
#include "r_driver/r_cg_cgc.h"
#include "r_driver/r_cg_intc.h"
#include "r_driver/r_cg_port.h"
#include "r_driver/r_cg_serial.h"
#include "r_driver/r_cg_timer.h"
#include "r_driver/r_cg_userdefine.h"
// RL78G13 includes
#include "ior5f100lg.h"
#include "ior5f100lg_ext.h"
#include "intrinsics.h"
// LCP development includes
#include "lcp_radio_driver.h"
#include "lcp_fsm.h"
#include "lcp_ax25.h"
#include "lcp_ax25.h"
#include "lcp_sensors_driver.h"
/* Set option bytes */
#pragma location = "OPTBYTE"
__root const uint8_t opbyte0 = 0xEFU;
#pragma location = "OPTBYTE"
__root const uint8_t opbyte1 = 0xFFU;
#pragma location = "OPTBYTE"
__root const uint8_t opbyte2 = 0xE8U;
#pragma location = "OPTBYTE"
__root const uint8_t opbyte3 = 0x84U;
/* Set security ID */
#pragma location = "SECUID"
__root const uint8_t secuid[10] =
    {0x00U, 0x00U, 0x00U, 0x00U, 0x00U, 0x00U, 0x00U, 0x00U, 0x00U, 0x00U};

int system_config (void);
void R_Systeminit(void);

void main (void) // LCP MAIN SOFTWARE
{
    system_config ();

    while(1)
    {
        lcp_state_machine ();
    }
}

/**
 * @brief System configuration for th GPIOs, SPI bus, Interruption and timers and the connected peripheral devices (sx1276 LoRa radio, etc..)
 */
int system_config (void)
{
    R_Systeminit(); // System setup and SPI00 configuration

    // SPI BUS
    // PINS: CLK(P10) / MISO(11)input / MOSI(12)output
    // DATA RATE: 1MHz
    // POLARITY: CLK starts in low, DATA is sampled in the DOWN edge of CLK
    // MSB First

    EI(); // Enable Interruptions
    R_INTC1_Start(); // INTC1 enable - PORT50 Rising Edge
    R_CSI00_Start(); // init SPI channel (00)

    // CHIP SELECT FOR RADIO DEVICE
    PM7_bit.no0 = 0; // PIN as OUTPUT
    PU7_bit.no0 = 1; // Pull-Up on
    CSS_RADIO_PORT = 1; // Start with High value

    // RADIO RESET
    PM7_bit.no1 = 0; // PIN as OUTPUT
    PU7_bit.no1 = 1; // Pull-Up on
    RESET_RADIO_PORT = 1; // Start with High value

    // CHIP SELECT FOR BMP280 DEVICE
    PM7_bit.no2 = 0; // PIN as OUTPUT
    PU7_bit.no2 = 1; // Pull-Up on
    CSS_BME_280_PORT = 1; // Start with High value

    // CHIP SELECT FOR GPS DEVICE
    PM7_bit.no3 = 0; // PIN as OUTPUT
    PU7_bit.no3 = 1; // Pull-Up on
    CSS_BME_280_PORT = 1; // Start with High value

    // BATTERY FAULT INPUT
    PM7_bit.no4 = 1; // PIN as INPUT
    PU7_bit.no4 = 1; // Pull-Up on

    // RADIO COMMUNICATION STATUS LED
    PM7_bit.no5 = 0; // PIN as OUTPUT
    PU7_bit.no5 = 1; // Pull-Up on
    LED_PORT = 0; // Start with Low value

    // POWER ON LED
    PM7_bit.no6 = 0; // PIN as OUTPUT
    PU7_bit.no6 = 1; // Pull-Up on
    PWR_ON_LED_PORT = 0; // Start with Low value

    // FAULT LED
    PM7_bit.no7 = 0; // PIN as OUTPUT
    PU7_bit.no7 = 1; // Pull-Up on
    FAULT_LED_PORT = 0; // Start with Low value

    // BATTERY SWITCH
    PM0_bit.no6 = 0; // PIN as OUTPUT
    PU0_bit.no6 = 1; // Pull-Up on
    BATTERY_SWITCH_PORT = 1; // Start with High value (1=MAIN, 0=BACKUP)

    // RESET BACKUP RL78
    PM0_bit.no5 = 0; // PIN as OUTPUT
    PU0_bit.no5 = 1; // Pull-Up on
    SECONDARY_MCU_RESET = 1; // Start with High value (1=BACKUP DISABLED, 0=BACKUP ENABLED)

    // REFERENCE SIGNAL FOR BACKUP RL78
    PM3_bit.no0 = 0; // PIN as OUTPUT
    PU3_bit.no0 = 1; // Pull-Up on
    MCU_ALIVE_PORT = 1; // Start with High value

    // DIO 0 - in TX: PacketSent Flag - in RX: PayloadReady Flag
    PM5_bit.no0 = 1; // INPUT - PIN50 set the INTP1 in Rising Edge
    PU5_bit.no0 = 0; // Pull-Up off
    // DIO_0_PORT

    // DIO 2 - can be used qith the interruption
    PM5_bit.no1 = 1; // INPUT - PIN51 set the INTP2 in Rising Edge
    PU5_bit.no1 = 0; // Pull-Up off


    FAULT_LED_PORT = 0;
    PWR_ON_LED_PORT	= 0;
    LED_PORT = 1;
    // Radio Register configuration for FSK packet mode
    // Data rate is 4.8kbps
    // Pkt size is 64 bytes
    radio_version_check(); // check if version matches (v12)
    radio_register_config (); // run configuration of sx1276 registers
    LED_PORT = 0;

    return (1);
}

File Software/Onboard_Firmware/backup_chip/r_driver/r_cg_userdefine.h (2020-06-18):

/*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
* Copyright (C) 2011, 2017 Renesas Electronics Corporation. All rights reserved.
***********************************************************************************************************************/

/***********************************************************************************************************************
* File Name    : r_cg_userdefine.h
* Version      : Applilet3 for RL78/G13 V2.04.00.03 [05 May 2017]
* Device(s)    : R5F100LE
* Tool-Chain   : IAR Systems iccrl78
* Description  : This file includes user definition.
* Creation Date: 16/02/2020
***********************************************************************************************************************/

#ifndef _USER_DEF_H
#define _USER_DEF_H

//#include "../lcp_radio_driver.h"
#include "../lcp_fsm.h"
//#include "../lcp_ax25.h"

#define CSS_RADIO_PORT          P7_bit.no0 // out
#define RESET_RADIO_PORT        P7_bit.no1 // out
#define CSS_BME_280_PORT        P7_bit.no2 // out
#define CSS_GPS_PORT            P7_bit.no3 // out
#define BATTERY_FAUL_PORT       P7_bit.no4 // in
#define LED_PORT                P7_bit.no5 // out
#define PWR_ON_LED_PORT         P7_bit.no6 // out
#define FAULT_LED_PORT          P7_bit.no7 // out

#define DIO_0_PORT              P5_bit.no0 // in - interrupt driven
#define DIO_2_PORT              P5_bit.no1 // in - interrupt driven
// #define DIO_2_PORT           P5_bit.no2  
// #define LED_PORT             P5_bit.no4

#define MCU_ALIVE_PORT          P3_bit.no0 // main - out // backup - in

#define SECONDARY_MCU_RESET     P0_bit.no5 // out
#define BATTERY_SWITCH_PORT     P0_bit.no6 // out

 /*
  *     SPI_CLK     P10
  *     SPI_MISO    P11
  *     SPI_MOSI    P12
  * 
  * 
  */
extern int spi_completion_flag;

extern lcp_communication_status_t com_status;
extern int timeout_flag;


#endif

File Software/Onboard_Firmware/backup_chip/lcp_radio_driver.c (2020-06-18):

/****************************************************************************/
/*                                                                          */
/* This Source Code Form is subject to the terms of the Mozilla Public      */
/* License, v. 2.0. If a copy of the MPL was not distributed with this      */
/* file, You can obtain one at http://mozilla.org/MPL/2.0/.                 */
/*                                                                          */
/****************************************************************************/

/*
 * This File is part of the LCP project
 */

/** 
 * @file lcp_radio_driver.c
 * 
 * @author Bruno Agusto Casu
 *
 * @revisor Bruno Duarte
 *
 * @brief Driver for the LCP radio device
 */


#include "string.h"
#include "stdio.h"
#include "stdlib.h"
// applilet includes
#include "r_driver/r_cg_macrodriver.h"
#include "r_driver/r_cg_adc.h"
#include "r_driver/r_cg_cgc.h"
#include "r_driver/r_cg_intc.h"
#include "r_driver/r_cg_port.h"
#include "r_driver/r_cg_serial.h"
#include "r_driver/r_cg_timer.h"
#include "r_driver/r_cg_userdefine.h"
// RL78G13 includes
#include "ior5f100lg.h"
#include "ior5f100lg_ext.h"
#include "intrinsics.h"
// LCP development includes
#include "lcp_radio_driver.h"

/**
 * @brief Function to write the sx1276 register via SPI bus
 * 
 * @param addr register address (7 bit)
 * @param data byte to be written in the register
 * 
 * @return current value in the target register
 */
uint8_t sx1276_write_register (uint8_t addr, uint8_t data)
{
    uint8_t tx_buff_ptr[2];
    uint8_t rx_buff_ptr[2];
    tx_buff_ptr[0] = (0x80) | addr;
    tx_buff_ptr[1] = data;

    CSS_RADIO_PORT = 0; // chip select down
    R_CSI00_Send_Receive(&tx_buff_ptr[0], 2, &rx_buff_ptr[0]); // SPI freq. is 1MHz - set down spi_completion_flag
    while (spi_completion_flag == 0)
        __no_operation(); // wait for transaction to be completed

    return rx_buff_ptr[1]; // return register current value
}

/**
 * @brief Function to read the radio (sx1276) register via SPI bus
 * 
 * @param addr 7 bit register address
 * 
 * @return current value in the target register
 */
uint8_t sx1276_read_register (uint8_t addr)
{
    uint8_t tx_buff_ptr[2];
    uint8_t rx_buff_ptr[2];
    tx_buff_ptr[0] = (0x7f) & addr;
    tx_buff_ptr[1] = 0;

    CSS_RADIO_PORT = 0; // chip select down
    R_CSI00_Send_Receive(&tx_buff_ptr[0], 2, &rx_buff_ptr[0]); // SPI freq. is 1MHz - set down spi_completion_flag
    while (spi_completion_flag == 0)
        __no_operation(); // wait for transaction to be completed

    return rx_buff_ptr[1];
}

/**
 * @brief Function to write one byte of data into the Radio FIFO
 * 
 * @param data byte to be written in the FIFO
 */
void sx1276_write_fifo (uint8_t data)
{
    sx1276_write_register(0, data);
}

/**
 * @brief Function to read one byte of data from the FIFO 
 * 
 * @return read byte from FIFO
 */
uint8_t sx1276_read_fifo (void)
{
    uint8_t data = sx1276_read_register(0);
        return data;
}

/**
 * @brief Switch the radio mode to Receiver
 */
void radio_tx_mode (void)
{
    sx1276_write_register (0x01, 0x00);
    sx1276_write_register (0x01, 0x03);
    system_delay_ms (5); // time to config the mode
}

/**
 * @brief Switch the radio mode to Transmitter
 */
void radio_rx_mode (void)
{
    sx1276_write_register (0x01, 0x00);
    sx1276_write_register (0x01, 0x05);
    int n = 0;
    while (DIO_2_PORT == 0 && n < 1000000)
    {
        __no_operation(); // hold until config is done
        n++;
    }
}

/**
 * @brief Switch the radio mode to Sleep mode
 */
void radio_sleep_mode (void)
{
    sx1276_write_register (0x01, 0x00);
    system_delay_ms (1);
}

 /**
  * @brief Configure all the radio register with the choosen operation parameters
  * \par
  * Data Transmission Mode: FSK \par
  * Carrier Frequency: 915MHz \par
  * Power output: 20dBm (100mW) Maximum output power \par
  * Preamble config: 1010 1010 (0xAA default) size of 16 bytes \par
  * Synchronization Word: enabled with size of 8 bytes \par
  * Packet configuration: Fixed Packet Length of 64bytes (payload)
  */
void radio_register_config (void)
{
    sx1276_write_register (0x01, 0x01); // set to Standby mode (for IQ and RSSI calibration Radio must be in Standby mode)
    sx1276_write_register (0x09, 0x00); // power output to zero

    // 915MHz carrier freq. config
    sx1276_write_register (0x06, 0xe4); // MSB of carrier freq. where f=R(23:0)*61,035
    sx1276_write_register (0x07, 0xc0);
    sx1276_write_register (0x08, 0x26); // LSB of carrier freq.

    // calibration process (IQ and RSSI calibration) for 915MHz radio frquency
    sx1276_write_register (0x3b, 0xc2);
    system_delay_ms (1);

    sx1276_write_register (0x09, 0xff); // power output to maximum value
    sx1276_write_register (0x01, 0x00); // put radio in sleep mode

    // set preamble size to 16 symbols
    sx1276_write_register (0x25, 0x00); // Preamble size MSB
    sx1276_write_register (0x26, 0x10); // preamble size LSB - must be the same for Tx and Rx!

    // Sync Configuration
    sx1276_write_register (0x27, 0x97); // Sync Config: set 8 bytes(max) to the Sync Word
    sx1276_write_register (0x28, 0x20); // Following byte are for the generation and confimation of the Sync Word (must be the same for Tx and Rx)
    sx1276_write_register (0x29, 0x20);
    sx1276_write_register (0x2a, 0x02);
    sx1276_write_register (0x2b, 0x27);
    sx1276_write_register (0x2c, 0x54);
    sx1276_write_register (0x2d, 0x52);
    sx1276_write_register (0x2e, 0x49);
    sx1276_write_register (0x2f, 0x45);

    // PACKET CONFIGURATION
    sx1276_write_register (0x30, 0x10); // fixed packet length / no encaoding / CRC on / Clear FIFO when CRC check fail / No address filtering
    sx1276_write_register (0x32, 0x40); // Payload length (LSB) = 64bytes
    sx1276_write_register (0x33, 0x8a); // Node addr for Tx and Rx (not being used)
    sx1276_write_register (0x35, 0x3f); // Interrupt for Start transmitting is FifoLevel with FifoThreshold = 63

    sx1276_write_register (0x40, 0x04); // DIO0 - 00 / DIO1 - 00 / DIO2 - 01
}

/**
 * @brief System delay function
 * 
 * @param time delay time in ms (max of 255ms)
 */
void system_delay_ms(unsigned char time)
{
    unsigned int temp;
    for (;time;time--)
        for (temp=32000/9;temp;temp--)
            __no_operation();
}
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

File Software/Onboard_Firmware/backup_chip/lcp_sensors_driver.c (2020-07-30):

/****************************************************************************/
/*                                                                          */
/* This Source Code Form is subject to the terms of the Mozilla Public      */
/* License, v. 2.0. If a copy of the MPL was not distributed with this      */
/* file, You can obtain one at http://mozilla.org/MPL/2.0/.                 */
/*                                                                          */
/****************************************************************************/

/*
 * This File is part of the LCP project
 */

/**
 * @file lcp_sensors_driver.c
 *
 * @author Bruno Agusto Casu
 *
 * @revisor Bruno Duarte
 *
 * @brief Driver for the attached sensros in the LCP
 */


#include "string.h"
#include "stdio.h"
#include "stdlib.h"
// applilet includes
#include "r_driver/r_cg_macrodriver.h"
//#include "r_driver/r_cg_adc.c"
#include "r_driver/r_cg_cgc.h"
#include "r_driver/r_cg_intc.h"
#include "r_driver/r_cg_port.h"
#include "r_driver/r_cg_serial.h"
#include "r_driver/r_cg_timer.h"
#include "r_driver/r_cg_userdefine.h"
// RL78G13 includes
#include "ior5f100lg.h"
#include "ior5f100lg_ext.h"
#include "intrinsics.h"
// LCP development includes
#include "lcp_radio_driver.h"
#include "lcp_fsm.h"
#include "lcp_ax25.h"
#include "lcp_sensors_driver.h"

uint8_t bmp280_read_register (uint8_t addr);
uint8_t bmp280_write_register (uint8_t addr, uint8_t data);

/**
 * @brief Function to operate all the ADC channels in the microcontroller
 *
 * @param data return the readings of the ADCs in for of a byte array
 */
void analog_sensors_read (uint8_t *data)
{
    uint16_t analog_value; //revised: (included)
    uint16_t * const channel_reading = &analog_value; //revised: (included)
    int data_position = 0;

    R_ADC_Set_OperationOn();

    ADS = _10_AD_INPUT_CHANNEL_16;
    R_ADC_Start();
    system_delay_ms (1);
    R_ADC_Get_Result(channel_reading);

    data[data_position] = (uint8_t)(analog_value>>8); //revised:
    data[data_position+1] = (uint8_t)(analog_value&0xFF); //revised:
    data_position += 2;
    R_ADC_Stop();

    ADS = _11_AD_INPUT_CHANNEL_17;
    R_ADC_Start();
    system_delay_ms (1);
    R_ADC_Get_Result(channel_reading);

    data[data_position] = (uint8_t)(analog_value>>8); //revised:
    data[data_position+1] = (uint8_t)(analog_value&0xFF); //revised:
    data_position += 2;
    R_ADC_Stop();

    ADS = _02_AD_INPUT_CHANNEL_2;
    R_ADC_Start();
    system_delay_ms (1);
    R_ADC_Get_Result(channel_reading);

    data[data_position] = (uint8_t)(analog_value>>8); //revised:
    data[data_position+1] = (uint8_t)(analog_value&0xFF); //revised:
    data_position += 2;
    R_ADC_Stop();

    ADS = _03_AD_INPUT_CHANNEL_3;
    R_ADC_Start();
    system_delay_ms (1);
    R_ADC_Get_Result(channel_reading);

    data[data_position] = (uint8_t)(analog_value>>8); //revised:
    data[data_position+1] = (uint8_t)(analog_value&0xFF); //revised:
    data_position += 2;
    R_ADC_Stop();

    ADS = _04_AD_INPUT_CHANNEL_4;
    R_ADC_Start();
    system_delay_ms (1);
    R_ADC_Get_Result(channel_reading);

    data[data_position] = (uint8_t)(analog_value>>8); //revised:
    data[data_position+1] = (uint8_t)(analog_value&0xFF); //revised:
    data_position += 2;
    R_ADC_Stop();

    ADS = _05_AD_INPUT_CHANNEL_5;
    R_ADC_Start();
    system_delay_ms (1);
    R_ADC_Get_Result(channel_reading);

    data[data_position] = (uint8_t)(analog_value>>8); //revised:
    data[data_position+1] = (uint8_t)(analog_value&0xFF); //revised:
    data_position += 2;
    R_ADC_Stop();

    ADS = _06_AD_INPUT_CHANNEL_6;
    R_ADC_Start();
    system_delay_ms (1);
    R_ADC_Get_Result(channel_reading);

    data[data_position] = (uint8_t)(analog_value>>8); //revised:
    data[data_position+1] = (uint8_t)(analog_value&0xFF); //revised:
    data_position += 2;
    R_ADC_Stop();

    ADS = _07_AD_INPUT_CHANNEL_7;
    R_ADC_Start();
    system_delay_ms (1);
    R_ADC_Get_Result(channel_reading);

    data[data_position] = (uint8_t)(analog_value>>8); //revised:
    data[data_position+1] = (uint8_t)(analog_value&0xFF); //revised:
    data_position += 2;
    R_ADC_Stop();

    ADS = _12_AD_INPUT_CHANNEL_18;
    R_ADC_Start();
    system_delay_ms (1);
    R_ADC_Get_Result(channel_reading);

    data[data_position] = (uint8_t)(analog_value>>8); //revised:
    data[data_position+1] = (uint8_t)(analog_value&0xFF); //revised:
    data_position += 2;
    R_ADC_Stop();

    ADS = _13_AD_INPUT_CHANNEL_19;
    R_ADC_Start();
    system_delay_ms (1);
    R_ADC_Get_Result(channel_reading);

    data[data_position] = (uint8_t)(analog_value>>8); //revised:
    data[data_position+1] = (uint8_t)(analog_value&0xFF); //revised:
    R_ADC_Stop();

    R_ADC_Set_OperationOff();
    // SEQUENCE OF DATA:
    // B19  B18  B17  B16  B15  B14  B13  B12  B11  B10  B9   B8   B7   B6   B5   B4   B3   B2   B1   B0
    // MSB  LSB  MSB  LSB  MSB  LSB  MSB  LSB  MSB  LSB  MSB  LSB  MSB  LSB  MSB  LSB  MSB  LSB  MSB  LSB
    // AMP  AMP  VCC  VCC  LDR5 LDR5 LDR4 LDR4 LDR3 LDR3 LDR2 LDR2 LDR1 LDR1 LDR0 LDR0 NTC1 NTC1 NTC0 NTC0
}
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
